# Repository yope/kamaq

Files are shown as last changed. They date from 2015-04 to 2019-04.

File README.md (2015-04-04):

Kamaq
=====

1. Introduction
---------------

Kamaq is a 3D-printer (FDM) controller software running on an embedded Linux
system. It is capable of controlling a RepRap-style 3D printer, but with
different electronics. Stepper motor control is done using a 8-channel (7.1)
USB audio device and some class-D audio amplifiers. Endstop switches are
monitored via GPIO inputs (interrupt-capable) and temperature control for
extruder and heated bed via standard hwmon-compatible ADC's and GPIO-outputs
for heater control. The software has a web-iterface for machine control and
monitoring. Why do it like this when there are already so many different hard-
and software projects dedicated to 3D printers (RepRap and all its
derivatives)?  Well, because as is the case with all engineers, I always know
better ;-)

2. Status of this project
-------------------------

This project is currently in heavy development. There are some bugs and missing
features, but overall the software can be (and has been) used for many
successful prints.
The software can control 4 motors (X, Y, Z and Extruder), read 3 endswitches
and control extruder- and heated-bed temperatures. The G-Code interpreter is
still very simple, but the software is already able to succesfully print
objects from a G-Code-file generated with cura or repsnapper.

3. Platform requirements
------------------------

Kamaq should be able to run on any embedded linux platform such as the beagle-
board, beagle-bone or the raspberry-pi with a suitable audio device, GPIO and
HWmon compatible A/D converters for temperature measurement.
The sound device should have twice the number of channels as the number of
motors that need to be controlled. For example a cheap 7.1 USB audio device
will be enough for controlling 4 stepper-motors.

4. Main application
-------------------

Of course the main goal for this project is controlling 3D-printer hardware,
such as the RepRap Prusa i3 for example, but it may also be adapted for other
applications requiring control of motors from G-Codes.

5. Required hardware
--------------------

5.1. Audio device
-----------------

The sound-card will work better if modified slightly, by shorting the DC-
blocking capacitors at the output. On many USB audio devices this is a
trivial task to do. For example the Sweex SC016 contains a C-Media CM6206
7.1 channel USB audio codec. Datasheets can easily be found via Google, and
they contain reference schematics that will be very similar to most
implementations of popular 7.1 USB audio devices that use this chip.
Most of the time they will use cheap through-hole electrolytic capacitors,
that are very easy to short out.

5.2. Audio amplifiers
---------------------

Bipolar 2-phase stepper-motors are best driven by a controlled current.
Although in theory, having a good model of the motor that takes into account
inductance and back-EMF at different speeds, one could calculate the correct
voltage-waveform to be applied to the motor windings and just use a voltage-
amplifier wich might be a little easier to build (specially when using class-D
amplifier IC's).
For my first hardware implementation, I built very simple class-B amplifiers
with current-feedback based on a bunch of TDA2030A I had laying around. This
version didn't require any motor modeling.
The second version which I am currently using is based on class-D audio
amplifier IC's, which save a lot of space and simplify the power supply
enormously. The class-D amplifiers lack current-feedback though, so I have
added rudimentary software support for voltage control also.

5.3. Heater control
-------------------

To control heater elements (such as for the extruder or the heated-bed of a
3D-printer), simple low-side switches with power-MOSFETS with very low-Rdson
will be perfect.
Temperature feedback is best implemented via simple A/D converters that support
HW-mon drivers, such as the ADS1015 from TI, which has mainline-linux support.

5.4. Hardware implementation
----------------------------

I have implemented all the needed hardware to control a 3D printer using this
software in very little time and effort. If there is enough interest I might
open-source the hardware (Kicad schematics and layout) too, but it is really
simple and straight-forward stuff right now hacked together in very little time.

6. Tools
--------

 * kamaq.py: Main application, starts the web-server.

 * grunner.py: This command-line tool can execude whole G-Code files or single
   movements by specifying relative distance on each axis (including extruder)
   on the command-line. It supports homing on endswitches and extruder
   temperature control. Currently not functional. Use the web-server instead.

 * set_current.py: Very simple tool that sets constant motor currents for all
   motors specified on the command-line. Can be used for adjusting motor
   current via the audio mixer. For each motor, two values are specified from
   -30000 to 30000, corresponding to the currents through each of the two
   coils. If less than 8 values (for 4 motors) are specified, the rest is
   assumed to be 0.

 * adjust_bed.sh: A script that aids in adjusting the for corners of the print-
   bed.

 * clean_extruder.sh: Move to a suitable position (high enough Z), heat
   extruder and start extruding a few cm. Deprecated. Will be removed soon
   probably.

7. TODO:
--------

Features that may or may not be implemented in the near or far future:

 * Implement pause and resume-from-layer-X.
 * Implemet G-code control via SSH or Serial port (to be able to use traditional
   printer control software).

8. Building Kamaq:
------------------

Install build dependencies (debian jessie or ubuntu):

 $ sudo apt-get install python3 cython3 libasound2-dev

Building (in-place, installation not supported yet):

 $ make

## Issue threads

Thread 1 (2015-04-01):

Automate preheat, home, start sequece

yope, 2015-04-01:
Implement automatic pre-heating of bed, then extruder, homing and start processing a file while unattended.

Closed 2015-07-26.

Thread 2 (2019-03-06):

project dead or alive

ekaggrat, 2019-03-06:
i just came accross this project via the reprap wiki .. it is very interesting to see a different way of doing things.  Is this project still under development or is it abandoned?

yope, 2019-03-06:
Thanks for asking.
This project is neither under active development, nor abandoned right now. I have my 3D printer powered by this hardware and software printing successfully for a few years now with excellent results. If I find bugs I fix them. If I need new features I'll implement them as soon as I find the time and motivation to do so.
Right now my printer is still using the second prototype hardware and not the latest boards I designed that include all the electronics on a single PCB. I need to find some time to get it assembled and tested.
It would be cool to see someone else try this hardware/software. I'd be willing to help with getting it to work. I'd also happily accept bug-reports and feature-requests.

ekaggrat, 2019-03-06:
ok great to hear that . I am still not clear as to how the steppers are run via the usb audio channels? and why instead of using the gpios directly

yope, 2019-03-07:
Stepper motors need a square-wave signal to move in whole steps. For 3D printing, one mostly wants to move the motors in micro-stepping mode, which divides the steps into smaller "sub-steps", where the controlling voltage (coil current actually) is not only on or off, but has intermediate levels. The finer the sub-steps, the more the signal looks like a sine-wave. So in the end you are driving the motors with an analog signal instead of a square-wave. In the case of Kamaq, these signals are generated with an 8-channel audio codec, and amplified with a couple of class-D power amplifiers instead of regular stepper motor drivers. The stepper motors are connected to the audio amplifiers (instead of a regular speaker).
The reason for doing this is two-fold:
1. A Linux systems is usually not hard real-time capable, so controlling GPIO pins at high speed and with precise timing is a challenge to do. That's why other printers usually use a small microcontroller to do the real-time work. In the case of Kamaq, the audio codec (with its buffers) does the real-time work of generating the driving signals. Producing sound with Linux is trivial.
2. Near infinite micro-stepping, limited only by the mechanical non-linearity of the steppers and the resolution of the audio codec (16-bit), enabling very fine control of motion with very low audible noise (the motors move almost silently).
An extra benefit of the class D audio amplifiers is that they tend to be more efficient than stepper motor drivers, so they don't even get warm.
Why use Linux to run 3D printer firmware? Well, Linux systems are much more powerful than microcontrollers used typically for 3D printer control, so I can have the luxury of writing the printer firmware in a high-level programming language such as Python for example, and easily have things like an integrated web-interface, camera streaming, remote monitoring, etc... which traditional 3D printers only get when pairing them with a Raspberry-Pi. Well, Kamaq actually let's you run the whole printer from a Raspberry-Pi without needing a microcontroller to do the motor control ;)

ekaggrat, 2019-03-07:
thanks ! that clears up a lot of things and seems to be a good approach. what hardware are you using it to run it currently? raspberry pi and discrete amplifiers?

yope, 2019-03-21:
Right now, a custom i.MX6 based processor board with a raspberry-pi compatible GPIO connector. You can also use a Raspberry-Pi 3. The first prototype hardware (which my printer is still using) had separate PCB's for each stepper motor, containing 2 class-D mono audio amplifier IC's on each.
The new hardware version contains everything on one single PCB that has the format if a Pi-hat. It can be connected to a Raspberry-pi GPIO connector, but needs a separate USB connection to the USB port and an external power supply to provide 12V for steppers, hot-end and heated bed.

Closed 2019-05-23.

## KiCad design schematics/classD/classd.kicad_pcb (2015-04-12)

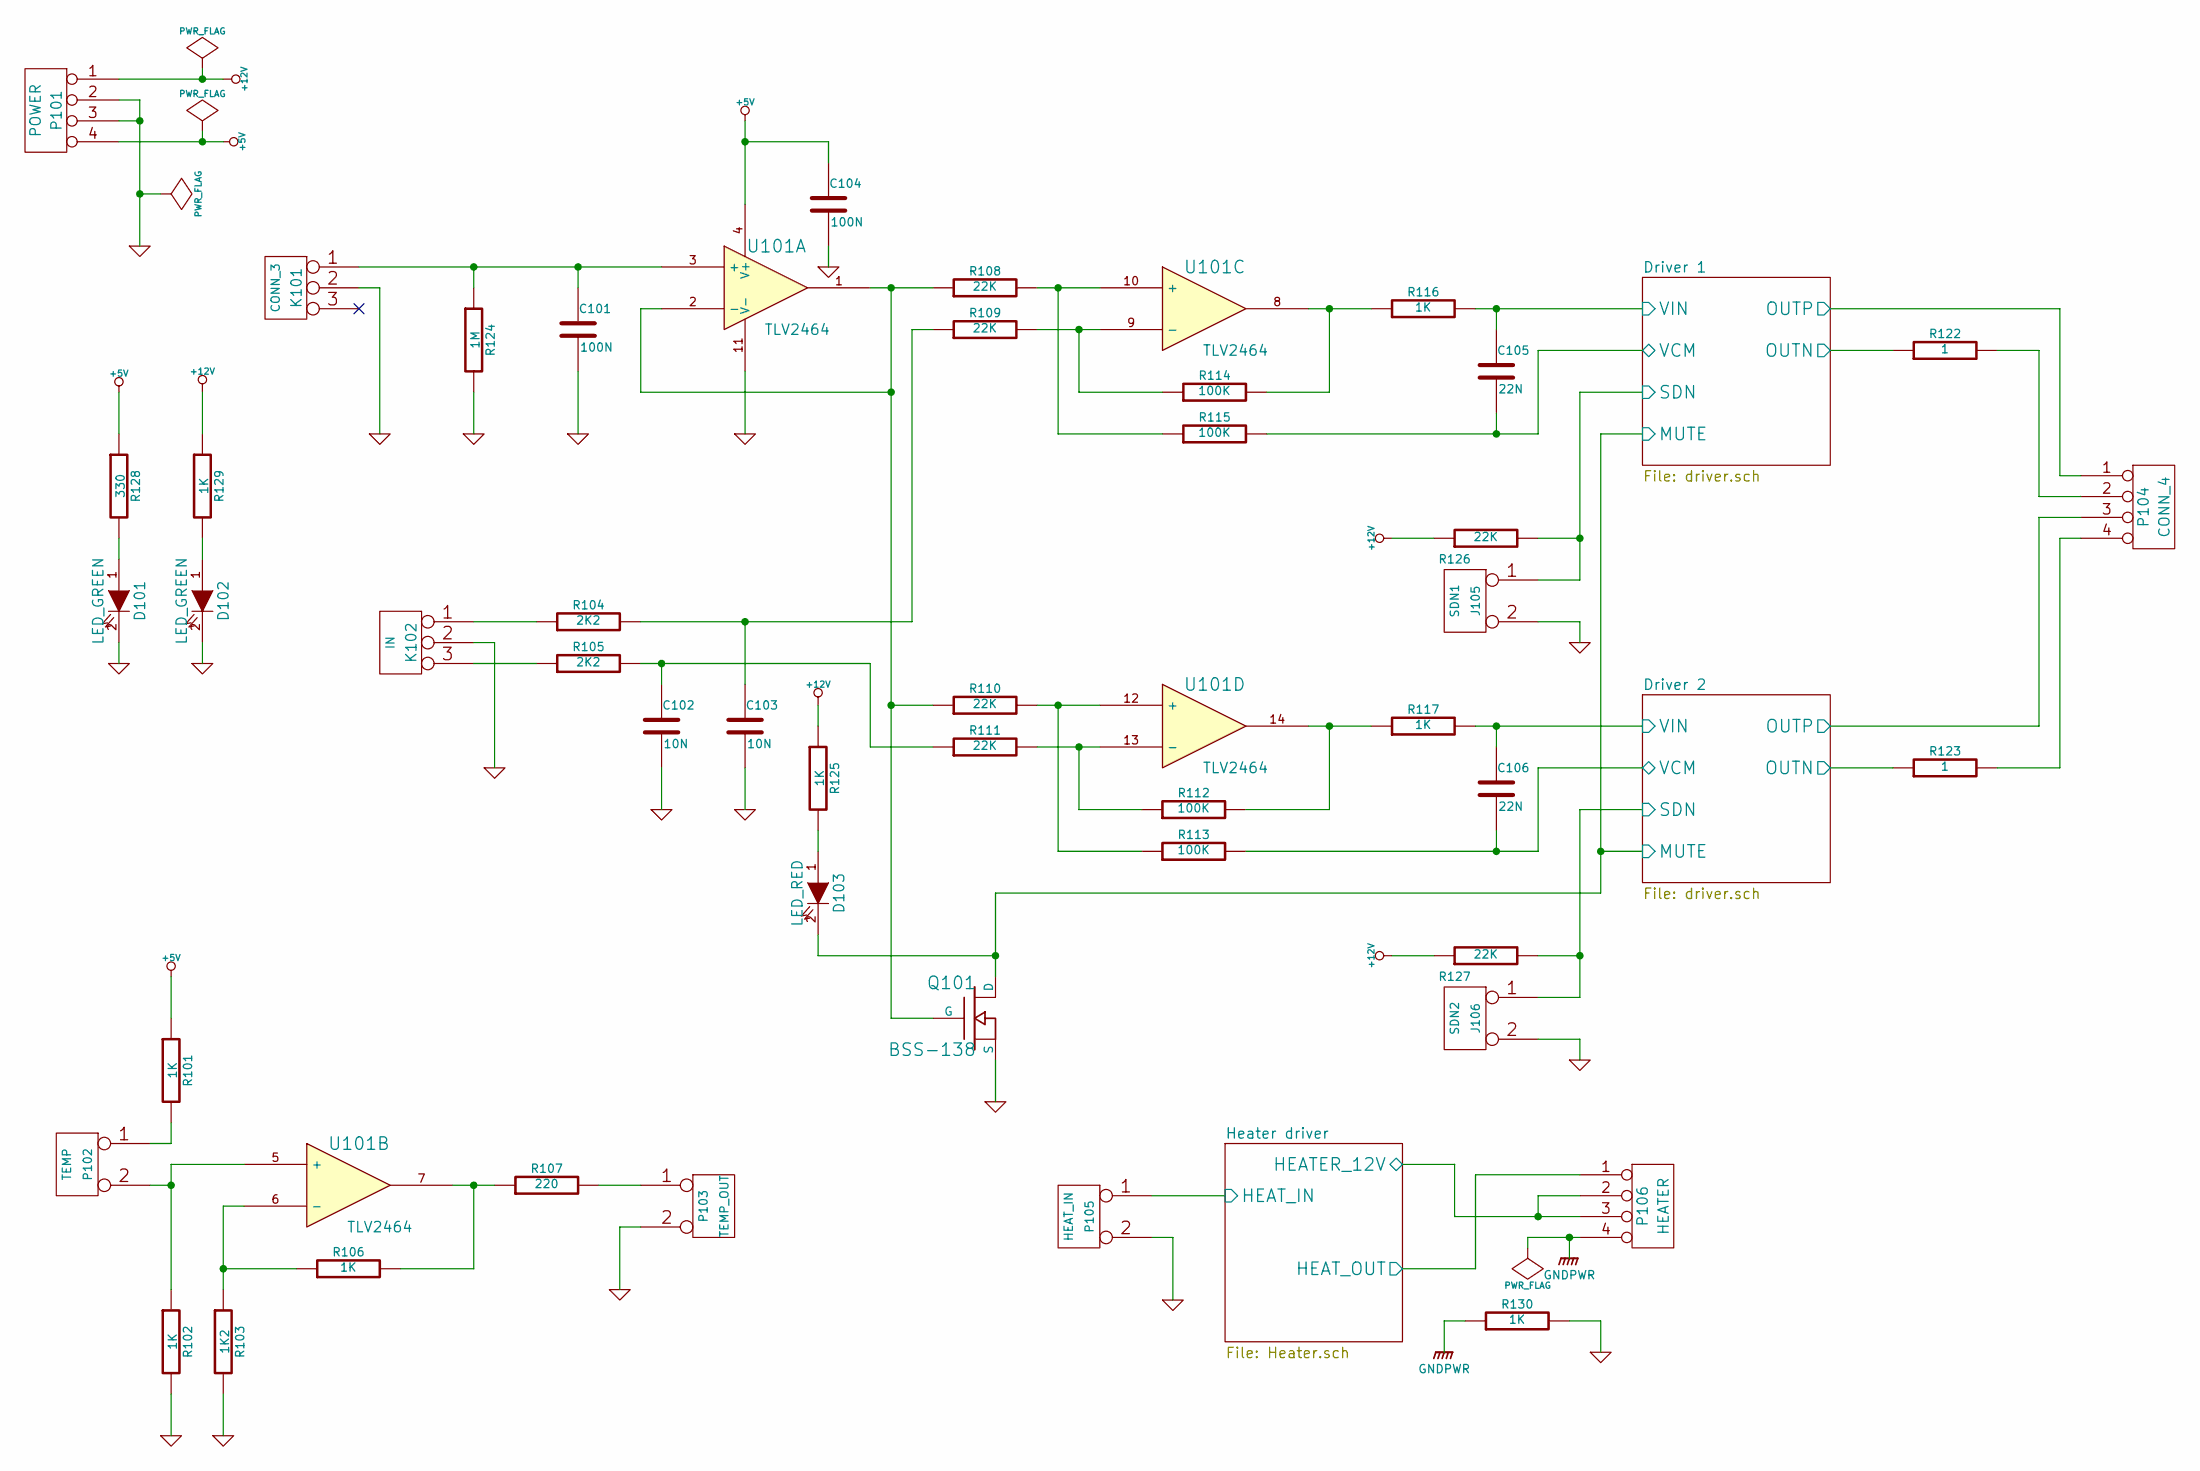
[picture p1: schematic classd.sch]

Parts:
C101, C104: 100N
C102, C103: 10N
C105, C106: 22N
D101, D102: LED_GREEN
D103: LED_RED
J105: SDN1
J106: SDN2
K101: CONN_3
K102: IN
P101: POWER
P102: TEMP
P103: TEMP_OUT
P104: CONN_4
P105: HEAT_IN
P106: HEATER
Q101: BSS-138
R101, R102, R106, R116, R117, R125, R129, R130: 1K
R103: 1K2
R104, R105: 2K2
R107: 220
R108, R109, R110, R111, R126, R127: 22K
R112, R113, R114, R115: 100K
R122, R123: 1
R124: 1M
R128: 330
U101: TLV2464

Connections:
+5V: C104.1, P101.4, R101.1, R128.1, U101.4 (V+); also elsewhere on the board
+12V: P101.1, R125.1, R126.1, R127.1, R129.1; also elsewhere on the board
/Driver 1/MUTE: D103.2 (K), Q101.D; also elsewhere on the board
/Driver 1/OUTN: R122.1; also elsewhere on the board
/Driver 1/OUTP: P104.1; also elsewhere on the board
/Driver 1/SDN: J105.1, R126.2; also elsewhere on the board
/Driver 1/VCM: C105.2, R115.2; also elsewhere on the board
/Driver 1/VIN: C105.1, R116.2; also elsewhere on the board
/Driver 2/OUTN: R123.1; also elsewhere on the board
/Driver 2/OUTP: P104.3; also elsewhere on the board
/Driver 2/SDN: J106.1, R127.2; also elsewhere on the board
/Driver 2/VCM: C106.2, R113.2; also elsewhere on the board
/Driver 2/VIN: C106.1, R117.2; also elsewhere on the board
/Heater driver/HEATER_12V: P106.2, P106.3; also elsewhere on the board
/Heater driver/HEAT_IN: P105.1; also elsewhere on the board
/Heater driver/HEAT_OUT: P106.1; also elsewhere on the board
GND: C101.2, C102.2, C103.2, C104.2, D101.2 (K), D102.2 (K), J105.2 (PM), J106.2 (PM), K101.2 (PM), K102.2 (PM), P101.2, P101.3, P103.2 (PM), P105.2 (PM), Q101.S, R102.2, R103.2, R124.2, R130.2, U101.11 (V-); also elsewhere on the board
GNDPWR: P106.4, R130.1; also elsewhere on the board
unnamed: P102.2 (PM), R102.1, U101.5 (+)
unnamed: P103.1, R107.2
unnamed: R106.2, R107.1, U101.7
unnamed: R103.1, R106.1, U101.6 (-)
unnamed: P102.1, R101.2
unnamed: D101.1 (A), R128.2
unnamed: D102.1 (A), R129.2
unnamed: D103.1 (A), R125.2
unnamed: R114.2, R116.1, U101.8
unnamed: Q101.G, R108.1, R110.1, U101.1, U101.2 (-)
unnamed: R109.2, R114.1, U101.9 (-)
unnamed: C103.1, R104.2, R109.1
unnamed: R108.2, R115.1, U101.10 (+)
unnamed: P104.4, R123.2
unnamed: P104.2, R122.2
unnamed: K102.3, R105.1
unnamed: C102.1, R105.2, R111.1
unnamed: K102.1, R104.1
unnamed: C101.1, K101.1, R124.1, U101.3 (+)
unnamed: R112.2, R117.1, U101.14
unnamed: R110.2, R113.1, U101.12 (+)
unnamed: R111.2, R112.1, U101.13 (-)

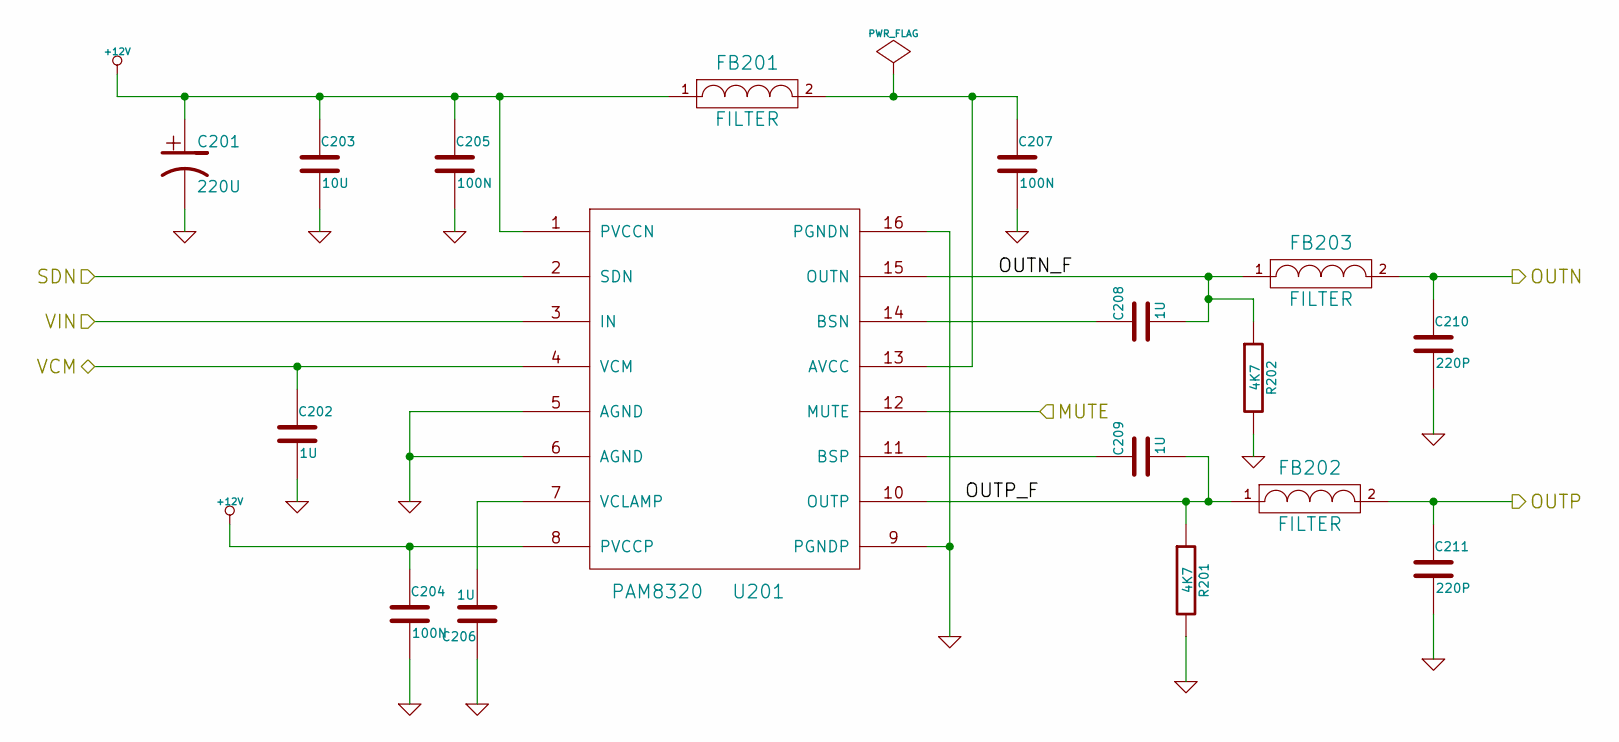
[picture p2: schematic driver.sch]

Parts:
C201: 220U
C202, C206, C208, C209: 1U
C203: 10U
C204, C205, C207: 100N
C210, C211: 220P
FB201, FB202, FB203: FILTER
R201, R202: 4K7
U201: PAM8320

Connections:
+12V: C201.1, C203.1, C204.1, C205.1, FB201.1, U201.1 (PVCCN), U201.8 (PVCCP); also elsewhere on the board
/Driver 1/MUTE: U201.12 (MUTE); also elsewhere on the board
/Driver 1/OUTN: C210.1, FB203.2; also elsewhere on the board
/Driver 1/OUTN_F: C208.2, FB203.1, R202.1, U201.15 (OUTN)
/Driver 1/OUTP: C211.1, FB202.2; also elsewhere on the board
/Driver 1/OUTP_F: C209.2, FB202.1, R201.1, U201.10 (OUTP)
/Driver 1/SDN: U201.2 (SDN); also elsewhere on the board
/Driver 1/VCM: C202.1, U201.4 (VCM); also elsewhere on the board
/Driver 1/VIN: U201.3 (IN); also elsewhere on the board
GND: C201.2, C202.2, C203.2, C204.2, C205.2, C206.1, C207.2, C210.2, C211.2, R201.2, R202.2, U201.5 (AGND), U201.6 (AGND), U201.9 (PGNDP), U201.16 (PGNDN); also elsewhere on the board
unnamed: C206.2, U201.7 (VCLAMP)
unnamed: C207.1, FB201.2, U201.13 (AVCC)
unnamed: C209.1, U201.11 (BSP)
unnamed: C208.1, U201.14 (BSN)

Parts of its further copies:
C301: 220U
C302, C306, C308, C309: 1U
C303: 10U
C304, C305, C307: 100N
C310, C311: 220P
FB301, FB302, FB303: FILTER
R301, R302: 4K7
U301: PAM8320

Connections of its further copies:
+12V: C301.1, C303.1, C304.1, C305.1, FB301.1, U301.1 (PVCCN), U301.8 (PVCCP); also elsewhere on the board
/Driver 1/MUTE: U301.12 (MUTE); also elsewhere on the board
/Driver 2/OUTN: C310.1, FB303.2; also elsewhere on the board
/Driver 2/OUTN_F: C308.2, FB303.1, R302.1, U301.15 (OUTN)
/Driver 2/OUTP: C311.1, FB302.2; also elsewhere on the board
/Driver 2/OUTP_F: C309.2, FB302.1, R301.1, U301.10 (OUTP)
/Driver 2/SDN: U301.2 (SDN); also elsewhere on the board
/Driver 2/VCM: C302.1, U301.4 (VCM); also elsewhere on the board
/Driver 2/VIN: U301.3 (IN); also elsewhere on the board
GND: C301.2, C302.2, C303.2, C304.2, C305.2, C306.1, C307.2, C310.2, C311.2, R301.2, R302.2, U301.5 (AGND), U301.6 (AGND), U301.9 (PGNDP), U301.16 (PGNDN); also elsewhere on the board
unnamed: C306.2, U301.7 (VCLAMP)
unnamed: C307.1, FB301.2, U301.13 (AVCC)
unnamed: C309.1, U301.11 (BSP)
unnamed: C308.1, U301.14 (BSN)

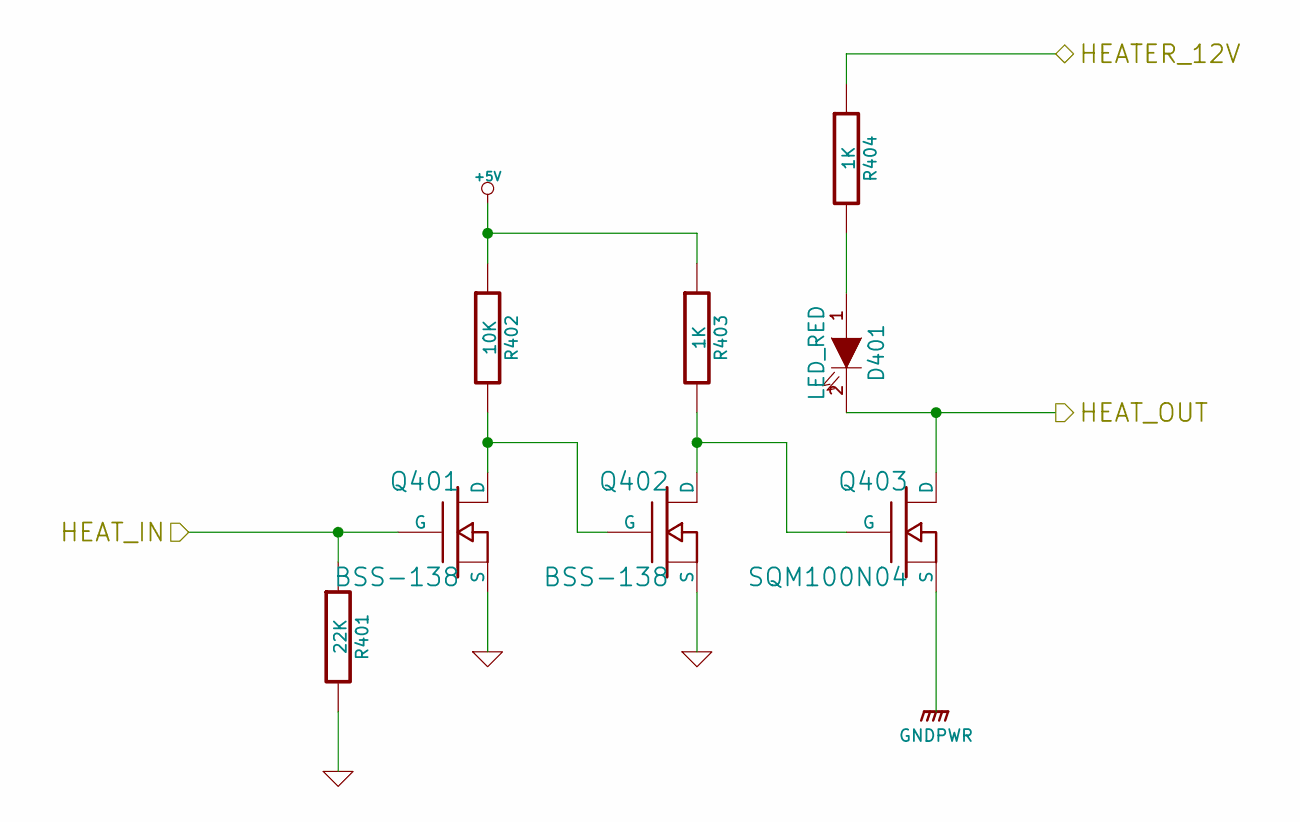
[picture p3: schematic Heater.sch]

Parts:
D401: LED_RED
Q401, Q402: BSS-138
Q403: SQM100N04
R401: 22K
R402: 10K
R403, R404: 1K

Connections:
+5V: R402.1, R403.1; also elsewhere on the board
/Heater driver/HEATER_12V: R404.1; also elsewhere on the board
/Heater driver/HEAT_IN: Q401.G, R401.1; also elsewhere on the board
/Heater driver/HEAT_OUT: D401.2 (K), Q403.2 (D); also elsewhere on the board
GND: Q401.S, Q402.S, R401.2; also elsewhere on the board
GNDPWR: Q403.3 (S); also elsewhere on the board
unnamed: Q402.D, Q403.1 (G), R403.2
unnamed: Q401.D, Q402.G, R402.2
unnamed: D401.1 (A), R404.2

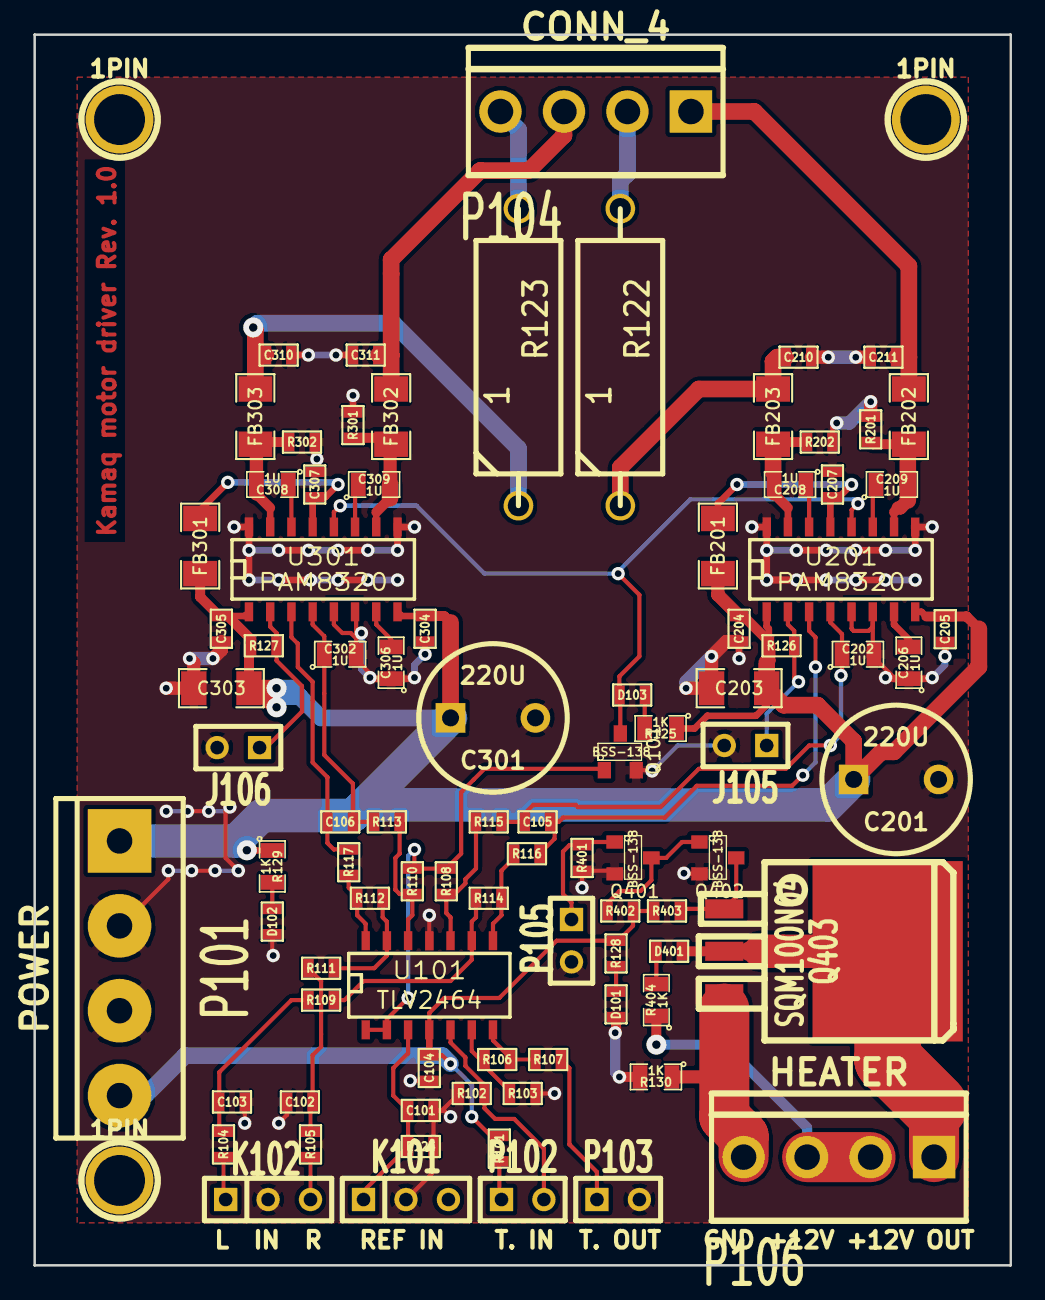
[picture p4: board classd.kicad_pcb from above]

Board: 2 copper layers, 58.4 x 73.7 mm, 92 parts (0 on the bottom side), 55 nets.

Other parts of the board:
1PIN, 1PIN#2, 1PIN#3: P***; 1pin

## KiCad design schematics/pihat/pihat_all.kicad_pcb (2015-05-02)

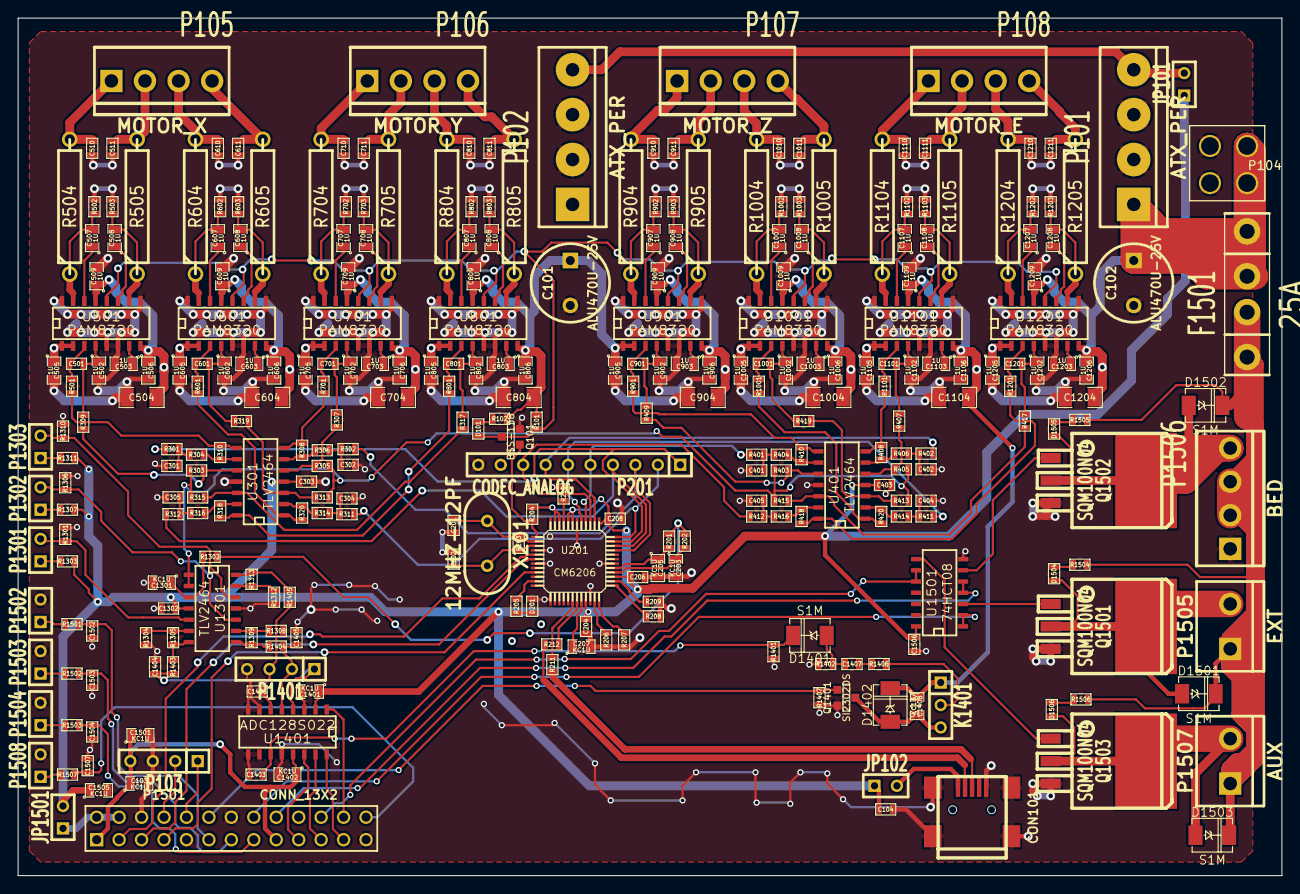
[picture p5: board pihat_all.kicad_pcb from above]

Board: 2 copper layers, 143.0 x 97.0 mm, 305 parts (0 on the bottom side), 192 nets.

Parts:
C101, C102: ALU470U-25V; C2V8
C103, C203, C205, C207, C1301, C1401, C1402, C1408, C1501, C1505: KC1U; SM0805
C104: KC10U; SM0603
C201, C202, C204, C206, C208, C303, C403, C1302, C1403, C1502, C1503, C1504, C1506, C1507: 100N; SM0603
C301, C302, C304, C305, C401, C402, C404, C405, C501, C601, C701, C801, C901, C1001, C1101, C1201, C1404, C1405, C1406, C1407: 10N; SM0603
C502, C503, C505, C506, C507, C508, C509, C602, C603, C605, C606, C607, C608, C609, C702, C703, C705, C706, C707, C708, C709, C802, C803, C805, C806, C807, C808, C809, C902, C903, C905, C906, C907, C908, C909, C1002, C1003, C1005, C1006, C1007, C1008, C1009, C1102, C1103, C1105, C1106, C1107, C1108, C1109, C1202, C1203, C1205, C1206, C1207, C1208, C1209: 1U; SM0805
C504, C604, C704, C804, C904, C1004, C1104, C1204: 10U; SM1206
C510, C511, C610, C611, C710, C711, C810, C811, C910, C911, C1010, C1011, C1110, C1111, C1210, C1211: 220P; SM0603
CON101: USB-MINI-B; USB_MINI_B
D101, D201, D1504, D1505, D1506: LED; SM0603
D1401, D1402, D1501, D1502, D1503: S1M; DO-214AC(SMA)
F1501: 25A; ATO257
JP101, JP102, JP1501: JUMPER; SIL-2
K1401: FAN; SIL-3
P101, P102: ATX_PER; bornier4
P103: SERIAL; SIL-4
P104: MOLEX-39-28-1043; MINIFIT-4
P105: MOTOR_X; MC4
P106: MOTOR_Y; MC4
P107: MOTOR_Z; MC4
P108: MOTOR_E; MC4
P201: CODEC_ANALOG; SIL-10
P1301: TEMP_EXT; SIL-2
P1302: TEMP_BED; SIL-2
P1303: TEMP_AUX; SIL-2
P1401: TEMP_ADC; SIL-4
P1501: CONN_13X2; pin_array_13x2
P1502: END_X; SIL-2
P1503: END_Y; SIL-2
P1504: END_Z; SIL-2
P1505: EXT; bornier2
P1506: BED; MC4
P1507: AUX; bornier2
P1508: END_L; SIL-2
Q101: BSS-138; SOT23GDS
Q1401: SI2302DS; SOT23GDS
Q1501, Q1502, Q1503: SQM100N04; TO263
R101, R102, R1301, R1302, R1303, R1305, R1306, R1307, R1309, R1310, R1311, R1313, R1402, R1406, R1501, R1502, R1503, R1504, R1505, R1506, R1507: 1K; SM0603
R201: N.P.; SM0603
R202: 0; SM0603
R203: 1M; SM0603
R204, R303, R304, R305, R306, R313, R314, R315, R316, R403, R404, R405, R406, R413, R414, R415, R416, R1401, R1407: 22K; SM0603
R205: 330; SM0603
R206, R207, R208, R209, R210, R307, R308, R309, R310, R317, R318, R319, R320, R407, R408, R409, R410, R417, R418, R419, R420: 10K; SM0603
R211, R212: 22; SM0603
R301, R302, R311, R312, R401, R402, R411, R412, R501, R601, R701, R801, R901, R1001, R1101, R1201: 2.2K; SM0603
R502, R503, R602, R603, R702, R703, R802, R803, R902, R903, R1002, R1003, R1102, R1103, R1202, R1203: 47K; SM0603
R504, R505, R604, R605, R704, R705, R804, R805, R904, R905, R1004, R1005, R1104, R1105, R1204, R1205: 0.5/3W; R6
R1304, R1308, R1312: 1.2K; SM0603
R1403, R1404, R1405: 47; SM0603
U201: CM6206; AB2_LQFP48
U301, U401, U1301: TLV2464; SO14E
U501, U601, U701, U801, U901, U1001, U1101, U1201: PAM8320; SO16E
U1401: ADC128S022; SO16E
U1501: 74HCT08; SO14E
X201: 12MHZ-12PF; HC-49V

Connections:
+3.3V: C103.1, C1402.1, C1501.1, P103.4, P1501.1, P1501.17, U1401.13
+5V: C104.1, C204.1, C206.1, C208.1, C303.1, C403.1, C1302.1, C1401.1, C1505.1, C1506.1, JP101.1, JP102.1, JP1501.2, R204.1, R1303.1, R1307.1, R1311.1, U201.21, U201.27, U201.37, U201.43, U201.44, U201.46, U201.47, U301.4, U401.4, U1301.4, U1401.2, U1501.14
+12V: C101.1, C102.1, C504.1, C505.1, C506.1, C509.1, C604.1, C605.1, C606.1, C609.1, C704.1, C705.1, C706.1, C709.1, C804.1, C805.1, C806.1, C809.1, C904.1, C905.1, C906.1, C909.1, C1004.1, C1005.1, C1006.1, C1009.1, C1104.1, C1105.1, C1106.1, C1109.1, C1204.1, C1205.1, C1206.1, C1209.1, C1408.1, D1402.2, F1501.1, K1401.1, P101.1, P102.1, P104.3, P104.4, R101.1, R102.1, U501.1, U501.2, U501.8, U501.13, U601.1, U601.2, U601.8, U601.13, U701.1, U701.2, U701.8, U701.13, U801.1, U801.2, U801.8, U801.13, U901.1, U901.2, U901.8, U901.13, U1001.1, U1001.2, U1001.8, U1001.13, U1101.1, U1101.2, U1101.8, U1101.13, U1201.1, U1201.2, U1201.8, U1201.13
/ADC/FAN_PWM: P1501.12, Q1401.G, R1407.1
/ADC/SPI_MISO: P1501.21, U1401.15
/ADC/SPI_MOSI: P1501.19, U1401.14
/ADC/SPI_SCLK: P1501.23, U1401.16
/ADC/TEMP_AUX: R1313.2, R1405.2, U1301.14
/ADC/TEMP_BED: R1309.2, R1404.2, U1301.8
/ADC/TEMP_EXT: R1305.2, R1403.2, U1301.7
/Audio Codec/CODEC_VBIAS: C205.1, R201.2, U201.29
/Audio Codec/CODEC_VREF: C203.1, R202.2, U201.28
/Audio Codec/MINT: P1501.7, U201.9
/Audio Codec/PDSW: Q101.G, R204.2, U201.1
/Audio Codec/SCL: P1501.5, U201.6
/Audio Codec/SDA: P1501.3, U201.5
/Audio Codec/USB_DM: CON101.2, R212.1
/Audio Codec/USB_DP: CON101.3, R211.1
/Audio Codec/VBIAS: R201.1, R202.1, R1302.1
/Biasing1/IN_A: P201.1, R301.1, U201.35
/Biasing1/IN_B: P201.2, R311.1, U201.36
/Biasing1/IN_C: P201.3, R302.1, U201.33
/Biasing1/IN_D: P201.4, R312.1, U201.34
/Biasing2/IN_A: P201.5, R401.1, U201.40
/Biasing2/IN_B: P201.6, R411.1, U201.41
/Biasing2/IN_C: P201.7, R402.1, U201.38
/Biasing2/IN_D: P201.8, R412.1, U201.39
/GPIO/GPIO7: C1507.1, P1501.26, R1507.1
/GPIO/GPIO17: C1502.1, P1501.11, R1501.1
/GPIO/GPIO22: C1504.1, P1501.15, R1503.1
/GPIO/GPIO23: P1501.16, U1501.1, U1501.2
/GPIO/GPIO24: P1501.18, U1501.4, U1501.5
/GPIO/GPIO25: P1501.22, U1501.9, U1501.10
/GPIO/GPIO27: C1503.1, P1501.13, R1502.1
/GPIO/SPI_nCE0: P1501.24, U1401.1
/GPIO/UART_RXD: P103.1, P1501.10
/GPIO/UART_TXD: P103.2, P1501.8
/Power Amp 1/OUTN: C510.1, P105.1, R504.2
/Power Amp 1/OUTP: C511.1, P105.2, R505.2
/Power Amp 1/VCM: C501.2, C502.1, R309.2, U501.4
/Power Amp 1/VIN: R310.2, R501.1, U301.8
/Power Amp 2/OUTN: C610.1, P105.3, R604.2
/Power Amp 2/OUTP: C611.1, P105.4, R605.2
/Power Amp 2/VCM: C601.2, C602.1, R319.2, U601.4
/Power Amp 2/VIN: R320.2, R601.1, U301.1
/Power Amp 3/OUTN: C710.1, P106.1, R704.2
/Power Amp 3/OUTP: C711.1, P106.2, R705.2
/Power Amp 3/VCM: C701.2, C702.1, R307.2, U701.4
/Power Amp 3/VIN: R308.2, R701.1, U301.7
/Power Amp 4/OUTN: C810.1, P106.3, R804.2
/Power Amp 4/OUTP: C811.1, P106.4, R805.2
/Power Amp 4/VCM: C801.2, C802.1, R317.2, U801.4
/Power Amp 4/VIN: R318.2, R801.1, U301.14
/Power Amp 5/OUTN: C910.1, P107.1, R904.2
/Power Amp 5/OUTP: C911.1, P107.2, R905.2
/Power Amp 5/VCM: C901.2, C902.1, R409.2, U901.4
/Power Amp 5/VIN: R410.2, R901.1, U401.8
/Power Amp 6/OUTN: C1010.1, P107.3, R1004.2
/Power Amp 6/OUTP: C1011.1, P107.4, R1005.2
/Power Amp 6/VCM: C1001.2, C1002.1, R419.2, U1001.4
/Power Amp 6/VIN: R420.2, R1001.1, U401.1
/Power Amp 7/OUTN: C1110.1, P108.1, R1104.2
/Power Amp 7/OUTP: C1111.1, P108.2, R1105.2
/Power Amp 7/VCM: C1101.2, C1102.1, R407.2, U1101.4
/Power Amp 7/VIN: R408.2, R1101.1, U401.7
/Power Amp 8/OUTN: C1210.1, P108.3, R1204.2
/Power Amp 8/OUTP: C1211.1, P108.4, R1205.2
/Power Amp 8/VCM: C1201.2, C1202.1, R417.2, U1201.4
/Power Amp 8/VIN: R418.2, R1201.1, U401.14
GND: C101.2, C102.2, C103.2, C104.2, C201.2, C202.2, C203.2, C204.2, C205.2, C206.2, C207.2, C208.2, C301.2, C302.2, C303.2, C304.2, C305.2, C401.2, C402.2, C403.2, C404.2, C405.2, C502.2, C503.2, C504.2, C505.2, C506.2, C509.2, C510.2, C511.2, C602.2, C603.2, C604.2, C605.2, C606.2, C609.2, C610.2, C611.2, C702.2, C703.2, C704.2, C705.2, C706.2, C709.2, C710.2, C711.2, C802.2, C803.2, C804.2, C805.2, C806.2, C809.2, C810.2, C811.2, C902.2, C903.2, C904.2, C905.2, C906.2, C909.2, C910.2, C911.2, C1002.2, C1003.2, C1004.2, C1005.2, C1006.2, C1009.2, C1010.2, C1011.2, C1102.2, C1103.2, C1104.2, C1105.2, C1106.2, C1109.2, C1110.2, C1111.2, C1202.2, C1203.2, C1204.2, C1205.2, C1206.2, C1209.2, C1210.2, C1211.2, C1301.2, C1302.2, C1401.2, C1402.2, C1403.2, C1404.2, C1405.2, C1406.2, C1501.2, C1502.2, C1503.2, C1504.2, C1505.2, C1506.2, C1507.2, CON101.5, CON101.6, CON101.7, CON101.8, CON101.9, D201.2, P101.2, P101.3, P102.2, P102.3, P103.3, P104.1, P104.2, P201.10, P1401.4, P1501.6, P1501.9, P1501.14, P1501.20, P1501.25, P1502.2, P1503.2, P1504.2, P1506.1, P1508.2, Q101.S, Q1401.S, Q1501.3, Q1502.3, Q1503.3, R206.2, R207.2, R208.2, R209.2, R210.2, R502.2, R503.2, R602.2, R603.2, R702.2, R703.2, R802.2, R803.2, R902.2, R903.2, R1002.2, R1003.2, R1102.2, R1103.2, R1202.2, R1203.2, R1301.2, R1304.2, R1306.2, R1308.2, R1310.2, R1312.2, R1401.1, R1402.2, R1407.2, U201.4, U201.7, U201.13, U201.22, U201.30, U201.42, U301.11, U401.11, U501.5, U501.6, U501.9, U501.16, U601.5, U601.6, U601.9, U601.16, U701.5, U701.6, U701.9, U701.16, U801.5, U801.6, U801.9, U801.16, U901.5, U901.6, U901.9, U901.16, U1001.5, U1001.6, U1001.9, U1001.16, U1101.5, U1101.6, U1101.9, U1101.16, U1201.5, U1201.6, U1201.9, U1201.16, U1301.11, U1401.3, U1401.7, U1401.8, U1401.9, U1401.10, U1401.12, U1501.7
MUTE: D101.2, Q101.D, R101.2, U501.12, U601.12, U701.12, U801.12, U901.12, U1001.12, U1101.12, U1201.12
unnamed: CON101.1, JP102.2
unnamed: JP101.2, P101.4, P102.4
unnamed: D101.1, R102.2
unnamed: C201.1, R203.1, U201.2, X201.1
unnamed: C207.1, U201.20
unnamed: R210.1, U201.45
unnamed: R209.1, U201.26
unnamed: R208.1, U201.25
unnamed: R207.1, U201.24
unnamed: C202.1, R203.2, U201.3, X201.2
unnamed: R206.1, U201.23
unnamed: R211.2, U201.18
unnamed: R212.2, U201.19
unnamed: D201.1, R205.2
unnamed: R205.1, U201.11
unnamed: R313.2, R319.1, U301.3
unnamed: R315.2, R317.1, U301.12
unnamed: C301.1, R301.2, R304.1
unnamed: C305.1, R312.2, R316.1
unnamed: C304.1, R311.2, R314.1
unnamed: R304.2, R310.1, U301.9
unnamed: R316.2, R318.1, U301.13
unnamed: R306.2, R308.1, U301.6
unnamed: R314.2, R320.1, U301.2
unnamed: R303.2, R309.1, U301.10
unnamed: R305.2, R307.1, U301.5
unnamed: C302.1, R302.2, R306.1
unnamed: R413.2, R419.1, U401.3
unnamed: R415.2, R417.1, U401.12
unnamed: C401.1, R401.2, R404.1
unnamed: C405.1, R412.2, R416.1
unnamed: C404.1, R411.2, R414.1
unnamed: R404.2, R410.1, U401.9
unnamed: R416.2, R418.1, U401.13
unnamed: R406.2, R408.1, U401.6
unnamed: R414.2, R420.1, U401.2
unnamed: R403.2, R409.1, U401.10
unnamed: R405.2, R407.1, U401.5
unnamed: C402.1, R402.2, R406.1
unnamed: C501.1, R501.2, U501.3
unnamed: C503.1, U501.7
unnamed: C508.2, R503.1, R505.1, U501.10
unnamed: C507.1, U501.14
unnamed: C508.1, U501.11
unnamed: C507.2, R502.1, R504.1, U501.15
unnamed: C603.1, U601.7
unnamed: C601.1, R601.2, U601.3
unnamed: C608.2, R603.1, R605.1, U601.10
unnamed: C607.1, U601.14
unnamed: C608.1, U601.11
unnamed: C607.2, R602.1, R604.1, U601.15
unnamed: C703.1, U701.7
unnamed: C701.1, R701.2, U701.3
unnamed: C708.2, R703.1, R705.1, U701.10
unnamed: C707.1, U701.14
unnamed: C708.1, U701.11
unnamed: C707.2, R702.1, R704.1, U701.15
unnamed: C803.1, U801.7
unnamed: C801.1, R801.2, U801.3
unnamed: C807.2, R802.1, R804.1, U801.15
unnamed: C807.1, U801.14
unnamed: C808.2, R803.1, R805.1, U801.10
unnamed: C808.1, U801.11
unnamed: C903.1, U901.7
unnamed: C901.1, R901.2, U901.3
unnamed: C907.2, R902.1, R904.1, U901.15
unnamed: C907.1, U901.14
unnamed: C908.2, R903.1, R905.1, U901.10
unnamed: C908.1, U901.11
unnamed: C1003.1, U1001.7
unnamed: C1001.1, R1001.2, U1001.3
unnamed: C1007.2, R1002.1, R1004.1, U1001.15
unnamed: C1007.1, U1001.14
unnamed: C1008.2, R1003.1, R1005.1, U1001.10
unnamed: C1008.1, U1001.11
unnamed: C1103.1, U1101.7
unnamed: C1101.1, R1101.2, U1101.3
unnamed: C1108.2, R1103.1, R1105.1, U1101.10
unnamed: C1107.1, U1101.14
unnamed: C1108.1, U1101.11
unnamed: C1107.2, R1102.1, R1104.1, U1101.15
unnamed: C1203.1, U1201.7
unnamed: C1201.1, R1201.2, U1201.3
unnamed: C1208.2, R1203.1, R1205.1, U1201.10
unnamed: C1207.1, U1201.14
unnamed: C1208.1, U1201.11
unnamed: C1207.2, R1202.1, R1204.1, U1201.15
unnamed: R1312.1, R1313.1, U1301.13
unnamed: P1303.2, R1310.1, U1301.12
unnamed: P1303.1, R1311.2
unnamed: P1302.1, R1307.2
unnamed: P1302.2, R1306.1, U1301.10
unnamed: R1308.1, R1309.1, U1301.9
unnamed: C1301.1, R1302.2, U1301.3
unnamed: R1304.1, R1305.1, U1301.6
unnamed: P1301.2, R1301.1, U1301.5
unnamed: P1301.1, R1303.2
unnamed: C1403.1, D1401.2, R1401.2, U1401.11
unnamed: C1407.1, D1401.1, R1402.1
unnamed: C1407.2, R1406.1
unnamed: K1401.2, R1406.2
unnamed: C1408.2, D1402.1, K1401.3, Q1401.D
unnamed: C1406.1, P1401.3, R1405.1, U1401.6
unnamed: C1405.1, P1401.2, R1404.1, U1401.5
unnamed: C1404.1, P1401.1, R1403.1, U1401.4
unnamed: D1506.1, R1506.2
unnamed: D1503.1, D1506.2, P1507.2, Q1503.2
unnamed: P1504.1, R1503.2
unnamed: P1503.1, R1502.2
unnamed: P1502.1, R1501.2
unnamed: D1501.1, D1504.2, P1505.2, Q1501.2
unnamed: D1502.1, D1505.2, P1506.4, Q1502.2
unnamed: D1505.1, R1505.2
unnamed: D1504.1, R1504.2
unnamed: D1501.2, D1502.2, D1503.2, F1501.2, P1505.1, P1506.2, P1506.3, P1507.1, R1504.1, R1505.1, R1506.1
unnamed: P1508.1, R1507.2
unnamed: JP1501.1, P1501.2, P1501.4
unnamed: Q1502.1, U1501.6
unnamed: Q1503.1, U1501.8
unnamed: Q1501.1, U1501.3
VBIAS: R303.1, R305.1, R313.1, R315.1, R403.1, R405.1, R413.1, R415.1, U1301.1, U1301.2

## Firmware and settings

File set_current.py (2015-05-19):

#!/usr/bin/env python3
#
# vim: set tabstop=4:
#
# Copyright (c) 2014 David Jander
#
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
from config import Config
from audiostep import audiostep
import sys

cfg = Config("kamaq.conf")
dim = cfg.settings["num_motors"]
vec = [0.0 for x in range(dim * 2)]
if len(sys.argv) > 1:
	for i in range(len(sys.argv) - 1):
		vec[i] = float(sys.argv[i + 1])
audiodev = cfg.settings["sound_device"]
audio = audiostep(cfg, audiodev, dim, None)
while True:
	audio.set_constant_current(vec)
audio.zero_output()
audio.close()

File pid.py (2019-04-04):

#!/usr/bin/env python
#
# vim: set tabstop=4:
#
# Copyright (c) 2014 David Jander
#
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
import time
import multiprocessing
import queue

def PidProcess(pid, cmdqueue):
	cmd = ""
	print("PID: Starting", pid.actuator.name, "...")
	while True:
		while not cmdqueue.empty():
			try:
				obj = cmdqueue.get()
			except queue.Empty:
				break
			if not "command" in obj:
				print("PID: Unknown command object:", repr(obj))
				continue
			cmd = obj["command"]
			if cmd == "shutdown":
				break
			else:
				print("PID: Unsupported command:", cmd)
		if cmd == "shutdown":
			break
		if not pid.iteration():
			break
	print("PID: Shutting down", pid.actuator.name, "...")

class PidController(object):
	def __init__(self, sensor, actuator, P, I, D, period=1.0):
		self.sensor = sensor
		self.actuator = actuator
		self.P = P
		self.I = I * period
		self.D = D / period
		self.period = period
		self.windup_limit = 100.0
		self.reset_pid()
		self.setvalue = multiprocessing.Value('d')
		self.outvalue = multiprocessing.Value('d')
		self.invalue = multiprocessing.Value('d')
		self.cmdqueue = multiprocessing.Queue()
		self.proc = multiprocessing.Process(target=PidProcess,
							args=(self, self.cmdqueue))
		self.spawned = False
		self.validate_previous = None
		self.sample_time = time.monotonic() + 0.2
		self.sample_count = 0
		self.sample_acc = 0
		self.error_state = False

	def reset_pid(self):
		self.integ = 0.0
		self.errq = queue.Queue()
		self.err0 = 0.0
		self.output = 0.0
		self.failure_timestamp = 0

	def set_setpoint(self, sp):
		self.setvalue.value = sp

	def validate_sensor(self, current):
		if current < 10.0:
			if not self.error_state:
				print("Temperature too low!")
			self.failure_timestamp = time.monotonic()
			return None
		if current > 300.0:
			if not self.error_state:
				print("Temperature too high!")
			self.failure_timestamp = time.monotonic()
			return None
		prev = self.validate_previous
		if prev is None:
			self.validate_previous = current
			return current
		if abs(prev - current) > 20.0:
			print("Temperature sensor unstable!")
			self.failure_timestamp = time.monotonic()
			self.validate_previous = current
			return None
		self.validate_previous = current
		return current

	def _get_tts(self):
		tts = self.sample_time - time.monotonic()
		return tts

	def _set_tts(self):
		tts = self.sample_time + 0.2
		if tts < time.monotonic():
			tts = time.monotonic() + 0.2
		self.sample_time = tts

	def _filter_sample(self):
		current = self.sensor.read()
		current = self.validate_sensor(current)
		if current is None:
			if not self.error_state:
				print("Temperature sensor failure detected. Shutting down heater!")
				self.error_state = True
			self.actuator.set_output(0)
			self.outvalue.value = 0
			time.sleep(2)
			return
		self.sample_acc += current
		self.sample_count += 1

	def sample(self, sec):
		while True:
			self._filter_sample()
			tts = self._get_tts()
			if tts >= sec:
				break
			if tts >= 0.0:
				time.sleep(tts)
			else:
				break
			sec -= tts
			self._set_tts()
		if sec > 0.0:
			time.sleep(sec)

	def iteration(self):
		if self.sample_count <= 0:
			if not self.error_state:
				print("PID: Error. Did not read any valid samples...")
			self.actuator.set_output(0)
			self.outvalue.value = 0
			self.sample(1)
			return True
		current = self.sample_acc / self.sample_count
		self.sample_acc = 0
		self.sample_count = 0
		self.invalue.value = current
		setpoint = self.setvalue.value
		if (time.monotonic() - self.failure_timestamp) < 10 or not setpoint:
			self.actuator.set_output(0)
			self.outvalue.value = 0
			self.sample(1)
			return True
		if self.failure_timestamp:
			print("Temperature sensor back to normal. Resuming heater.")
			self.error_state = False
			self.reset_pid()
		err = setpoint - current
		derr = err - self.err0
		self.errq.put(err)
		if self.errq.qsize() < 3:
			self.err0 = err
		else:
			self.err0 = self.errq.get()
		self.integ += err
		if self.integ > self.windup_limit:
			self.integ = self.windup_limit
		if self.integ < -self.windup_limit:
			self.integ = -self.windup_limit
		self.output = self.P * err + self.I * self.integ + self.D * derr
		if self.output > 1.0:
			self.output = 1.0
		if self.output < 0.0:
			self.output = 0.0
		ontime = self.output * self.period
		if ontime > 0.0:
			self.actuator.set_output(1)
		self.sample(ontime)
		if ontime < self.period:
			self.actuator.set_output(0)
			self.sample(self.period - ontime)
		self.outvalue.value = self.output
		return True

	def get_output(self):
		return self.outvalue.value

	def get_input(self):
		return self.invalue.value

	def spawn(self):
		self.proc.start()
		self.spawned = True

	def shutdown(self):
		if not self.spawned:
			return
		self.cmdqueue.put({"command": "shutdown"})
		self.proc.join()
		self.actuator.set_output(0)

if __name__ == "__main__":
	import signal, sys
	from temp100k import Thermistor100k
	from hwmon import ScaledSensor
	from config import Config
	from gpio import GPOutput
	s = ScaledSensor(Config("kamaq.conf"), "EXT")
	t = Thermistor100k(s)
	o = GPOutput("heater_EXT")
	p = PidController(t, o, 0.2, 0.002, 0.5)
	def signal_handler(signal, frame):
		print('You pressed Ctrl+C!')
		p.shutdown()
		sys.exit(0)
	signal.signal(signal.SIGINT, signal_handler)
	p.spawn()
	sp = 230.0
	p.set_setpoint(sp)
	while True:
		print("Temp =", t.read(), "setpoint =", sp, "Ouput =", p.get_output())
		time.sleep(1.0)
	p.shutdown()

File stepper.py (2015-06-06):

#
# Copyright (c) 2014 David Jander
#
# vim: set tabstop=4:
#
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
from audiostep import audiostep
from gpio import AsyncGPInput

class StepperCluster(object):
	def __init__(self, audiodev, dim, cfg, esw):
		self.cfg = cfg
		self.invert = [1 - int(x) * 2 for x in cfg.settings["invert_motor"]]
		self.audio = audiostep(cfg, audiodev, dim, esw)
		cfb = self.cfg.settings["current_feedback"]
		if cfb:
			self.audio.set_amplitude_dc(1.0)
		else:
			self.audio.set_amplitude_dc(0.3)
		self.dim = dim
		self.set_speed_scale(1.0)
		self.set_max_feedrate(cfg.settings["max_feedrate"] / 60.0)

	def connect_cmd_buffer(self, buf):
		self.audio.connect_cmd_buffer(buf)

	def pull_cmd_buffer(self):
		return self.audio.pull_cmd_buffer()

	def flush_queue(self):
		self.audio.flush_queue()

	def set_speed_scale(self, ss):
		self.speed_scale = ss
		self.audio.set_speed_scale(ss)

	def set_max_feedrate(self, limit):
		if limit:
			self.max_feedrate = limit
		self.audio.set_max_feedrate(limit)

	def handle_command(self, obj):
		cmd = obj[0]
		pos = obj[1]
		if cmd == "feedrate":
			rate = pos
			self.set_feedrate(rate)
		elif cmd == "feedrate3":
			rate = pos
			self.set_feedrate3(*rate)
		elif cmd == "position":
			self.set_destination(pos)
		elif cmd == "set_position":
			if pos is None:
				self.audio.set_home()
			else:
				self.audio.set_position(pos)
		else:
			print("SC: Unknown object:", repr(obj))

	def set_feedrate(self, rate):
		self.audio.set_feedrate(rate, rate, rate)

	def set_feedrate3(self, begin, high, end):
		self.audio.set_feedrate(begin, high, end)

	def set_destination(self, pos):
		self.audio.set_destination(pos)

	def get_position(self):
		return self.audio.get_position()

	def set_position(self, pos):
		self.audio.set_position(pos)

	def process_one_move(self):
		self.audio.process_one_move()

	def zero_output(self):
		self.audio.zero_output()

	def close(self):
		self.audio.close()

	def stop(self):
		self.audio.stop()

	def restart(self):
		self.audio.restart()

	def cancel_destination(self):
		self.audio.cancel_destination()

	def fileno(self):
		return self.audio.fileno()

	def write_more(self):
		return self.audio.write_more()

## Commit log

2014-07-22 stepper: Initial commit of stepper test class
2014-07-22 stepper: Started writing Stepper and StepperCluster classes
2014-07-28 stepper: rewrite speed-based to steps-based
    Implemented line drawing algorithm
2014-07-28 stepper: Implemented main loop and position callback
    WIP
2014-08-01 Added move and gcode modules and converted stepper.py to cython
2014-08-02 Rewrote stepper.pyx in C and created new interface
    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
2014-08-17 config.py: Corrected steps_per_mm and added sound_rate constant
    [config.py]
2014-08-17 stepper.py: Added new StepperCluster class as wrapper around audiostep
2014-08-22 Added set_current.py tool
    This tool can be used for calibrating output current/voltage
2014-09-01 audiostep: Implemented minimal write function to be used with asycore
    push_more_audio_data() will loop over main_iteration() until at least some
    audio data has been written to the audio device.
2014-09-06 Asyncore rewrite
    Added preliminary support for reading endstop switches.
    GRunner now uses the python asyncore module for handling audio data and
    GPIO's at the same time.
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2014-09-14 Add preliminary support for hwmon temperature sensor
    Added support for reading temperature from a 100k thermistor connected via
    an opamp to a hwmon-based ADC
2014-09-18 Added PID controller module
2014-09-24 config.py: Corrected calibration defauls
    To reflect a change in the measurement circuits.
    [config.py]
2014-09-24 PID: Added multiprocessing support to PID regulator
2014-09-24 grunner: Added preliminary support for temperature control.
2014-09-26 temp100k: Extend temperature table to 300 degrees C.
2014-09-28 config.py: Corrected steps per mm data for Z and E motors
    Changed max_speed vector parameter for max feedrate scalar
    [config.py]
2014-09-28 gcode: added support for suppressing extruder movements
    This is specially suited for "cold" test runs.
2014-09-28 Grunner: Corrected feedrates for other than X/Y motors
    Added --no-extrusion parameter and implemented proper feedrate limitation.
    [grunner.py, stepper.py]
2014-09-28 Added clean_extruder shell script.
    Run this prior to printing, to heat up the extruder and clean unclog it.
2014-10-01 move: Simplified homing algorithm
2014-10-10 clean_extruder.sh: added command-line options for more modes
    Short mode and no-xyz-movements mode.
    Also adjusted extruder speed.
2014-10-27 grunner.py: Implemented support for heated bed
2014-11-05 Fix vim modelines position
    [config.py, gcode.py, gpio.py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]
2014-12-20 audiodev: Add support for amplifiers without current feedback
    Introduce very simplistic motor modeling by assuming some arbitrary
    attenuation at higher frequencies. This will be compensated by just
    lowering the output gain at DC.
2014-12-20 config: Reduce maximum feedrate slightly
    The feedrate is high enough anyway. This permits reducing Z current a
    little
2014-12-20 temp100: Correct scaling factors for new hardware version
    [config.py, temp100k.py]
2014-12-20 Add script to aid adjusting printer-bed screws
2014-12-27 grunner.py: Added missing option to help
    [grunner.py]
2014-12-27 stepper.py: Fixed self.invert calculation.
    This fixes endstop detection.
    [stepper.py]
2014-12-27 Improved voltage mode current scaling
2014-12-27 audiodev.c: Fixed voltage mode
2014-12-27 clean_extruder.sh: Added heated bed setpoint option
2014-12-27 Decreased Z speed while calibrating home position
    If Z current setting is on the lower side, high speed increases chances of
    step skipping.
2014-12-28 pid.py: Implemented basic safety functions
    Detect a temperature sensor- or measurement circuit defect and turn off
    the corresponding heater. This is by no means a safety function that
    should be trusted blindly, but it can reduce the chances of fire a bit.
2014-12-28 grunner.py: Change PID parameters and setpoint threshold
2014-12-28 move.py: Tweaked Z homing
2014-12-28 Straightforward python 3 coversion
    Just applied 2to3 and hand-fixed three string-bytes conversions
    Code seems to work fine.
    [config.py, gcode.py, gpio.py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]
2015-01-16 pid.py: Add get_input() method
2015-01-18 stepper.py: Add support for idle mode
    When idle outputs are zeroed. This happens after EOF.
2015-01-18 monkeypatch.py: Added missing import math
    [monkeypatch.py]
2015-01-18 gpio.py: Cleanup and fix enable/disable exceptions
    [gpio.py]
2015-01-18 gcode.py: Fix S-code parsing
    [gcode.py]
2015-01-18 gcode.py: Fix home (G28) and set-home commands (G92)
    [gcode.py]
2015-01-18 gcode.py: Fix parsing non-code arguments
    [gcode.py]
2015-01-18 grunner.py: Fix bugs introduced by webui
    [grunner.py]
2015-01-18 stepper.py: Fix home command
    [stepper.py]
2015-01-23 pid.py: Avoid reading input value again from main thread
    [pid.py]
2015-01-23 printer.py: WIP: support for heater-extruder timeout
2015-01-25 webui/printer: Re-write around central printer class part 1
    WIP.
    The command-line interface will be deprecated in favor of the web-interface
    with the printer class as central piece. Later a new command-line
    interface can be added again.
2015-01-25 grunner.py: Fix broken import statement
    [grunner.py]
2015-01-28 gcode.py: Avoid examinating line outside of process function
    [gcode.py, printer.py]
2015-01-28 gcode.py: Fix code M104
    [gcode.py]
2015-01-28 gcode.py: Fix zero_extruder for relative mode
    [gcode.py]
2015-01-28 webui: Implemented many more functions
    The html interface is now fully functional for basic printing.
    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
2015-02-04 gcode.py: Fix G92 (set position) part 1
    [gcode.py]
2015-02-07 gcode.py: Fix layer_count parsing typo
    [gcode.py]
2015-02-07 priter.py: Implement temperature fail timeout
    [printer.py]
2015-02-07 stepper.py: Decrease maximum acceleration
    This is temporary, but makes movements a lot smoother on my i3.
    Once vector interpolation is in place, this will not be necessary
2015-02-21 Implement proper position update on stop and reset printer function
    [gcode.py, printer.py, stepper.py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]
2015-02-25 pid.py: Bugfix: unstable temperature sensor fault never recovers
    [pid.py]
2015-03-01 gcode: Fix G92 (set position)
    [gcode.py, stepper.py]
2015-03-01 webui: Added "Ignore Endstop" checkbox
2015-03-15 gcode.py: Fix bug in home (G28) command
    [gcode.py]
2015-03-15 kamaq.py: Fix renaming leftover
    [kamaq.py]
2015-03-15 printer.py: Reset move on EOF
    [printer.py]
2015-04-04 webui: Implement auto button
    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
2015-04-08 WIP: Rewrite movement command processing and interpolation in cython
    If we want to support weaker processors, such as the ARM11 core in the
    original raspberry pi, we need to optimize some critical code paths.
    This is a first attempt at speeding things up a little.
2015-04-08 hwmon.py: Don't just crash if our platform doesn't have a hwmon device
    [hwmon.py]
2015-04-12 Added rev. 1.0 kicad schematics and layout sources
    [Heater.sch, classd.kicad_pcb, classd.sch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]
2015-05-02 Initial commit of raspberry-pi hat for Kamaq
    [adc.sch, biasing.sch, codec.sch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]
2015-05-02 pihat: Added autolevel endstop
    As suggested by Jeremy Wuitschick
    [gpio.sch, pihat_all.kicad_pcb]
2015-05-02 pihat: missing annotation changes
    [biasing.sch, gpio.sch]
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2015-05-10 pid: Implemented sample averaging
    Feedback samples are measured 5 times per second and averaged
2015-05-10 stepper: Fixed max feedrate limiting
    [stepper.py]
2015-05-13 printer.py: Fix queue overrun on last command in stream
    [printer.py]
2015-05-17 audiostep: Raise exception if opening audio device fails
2015-05-17 gcode: BUGFIX: Fix G92 crash
    [gcode.py]
2015-05-19 set_current.py: Fix for new audiostep class args
    [set_current.py]
2015-06-03 Add basic support for temperature setting g-codes
    Adds support for G109, G116, G140, G190 and fixes G104
    [gcode.py, printer.py]
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2015-06-06 Implement abort button
    Does the same as stop, but without lifting the head
2015-07-11 hwmon: catch I/O errors when reading from HWMON device
    [hwmon.py]
2015-07-11 pid: fix shutdown issues.
    [pid.py]
2015-08-02 Added simple smartphone webinterface
    This is a simple low-bandwidth UI intended for remote mobile monitoring
    over the internet. It doesn't show graphs nor real-time position update.
    [webui.py]
2015-08-02 gcode: Fixed lines with comments being ignored in gcode.
    [gcode.py]
2015-08-02 printer: Set better heater policy defaults
    This had been changed on the webui already in previous commits.
2017-05-09 move.pyx: Always enable endstops when homing
    Avoid crashing into the build-plate if endstops had been disabled before.
2017-06-02 vector.pxy: Increase jerkiness a little to improve print quality
    This improves print quality (and retraction) at a nigligible expense of
    slightly jerkier printer movements.
2018-04-17 Add support for Z-offset trimming while printing
    This feature permits to tweak layer adhesion (for example when using
    buildtak) during the first layer.
2019-04-04 pid.py: Don't repeatedly report error conditions
    If printer power is off, this can cause significant amount of log messages
    if stdout is logged to a file.
    [pid.py]
2019-04-04 html: js: ui.js: Draw heated bed rectangle at the same place as the plot

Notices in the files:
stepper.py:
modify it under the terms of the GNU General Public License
